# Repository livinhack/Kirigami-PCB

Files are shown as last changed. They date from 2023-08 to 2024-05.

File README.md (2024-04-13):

# Kirigami PCB Mod

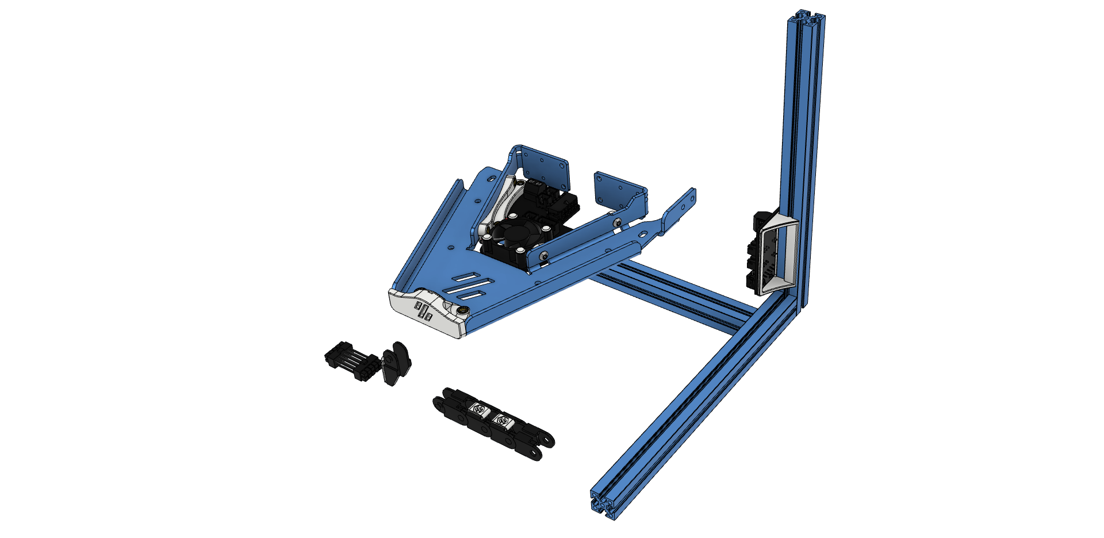
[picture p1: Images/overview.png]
Overview of the PCB's Title


This mod adds two PCBs ([Frame PCB](#frame-pcb), [Kirigami PCB](#kirigami-pcb)) and a cable ([Cable](#cable-and-chain)) to the V0.1/V0.2 that can aid in wire management and routing.

There are also optional things like a [Bed Fan](https://github.com/livinhack/Kirigami_PCB/tree/main/Optional/Bed_Fan) or a [Kirigami-Front](https://github.com/livinhack/Kirigami_PCB/tree/main/Optional/Front).

----

# Frame PCB
The frame PCB mounts on the side in the electronics bay of the printer and combines all cables into a single 10 pin Micro-Fit 3.0 connector. (With neopixel loop-through.)

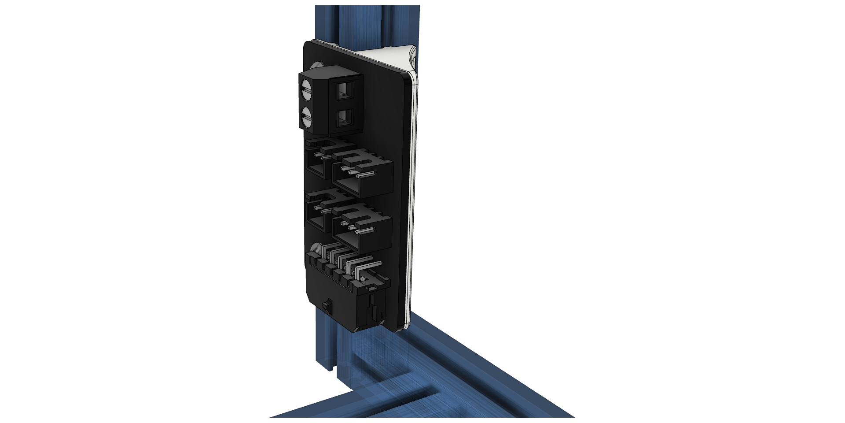
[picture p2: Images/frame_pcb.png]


## Frame PCB BOM
| Part | Quantity V1/V2 | Notes | LCSC Part Number | Link |
| --- | :-: | --- | --- |--- |
| 10 Pin Socket (Right Angle) | 1 | MOLEX 430451000 | C122421 | [lcsc](https://www.lcsc.com/product-detail/Wire-To-Board-Wire-To-Wire-Connector_MOLEX-430451000_C122421.html) |
| 2 pin JST XH | 2 | 2.5mm pitch | C158012 | [lcsc](https://lcsc.com/product-detail/Wire-To-Board-Wire-To-Wire-Connector_JST-Sales-America-B2B-XH-A-LF-SN_C158012.html) |
| 3 pin JST XH | 2 | 2.5mm pitch | C144394 | [lcsc](https://lcsc.com/product-detail/Wire-To-Board-Wire-To-Wire-Connector_JST-Sales-America-B3B-XH-A-LF-SN_C144394.html) |
| Screw Terminal | 1 | 5.08mm pitch | | [digikey](https://www.digikey.de/en/products/detail/metz-connect-usa-inc/31101102/7794830) |
| Screw M3x8 | 2 | | | |
| Nut M3 | 2 | | | |
----

# Kirigami PCB

Mounted on the Kirigami bed mount, this breaks out the 10 pin harness into all needed connectors.

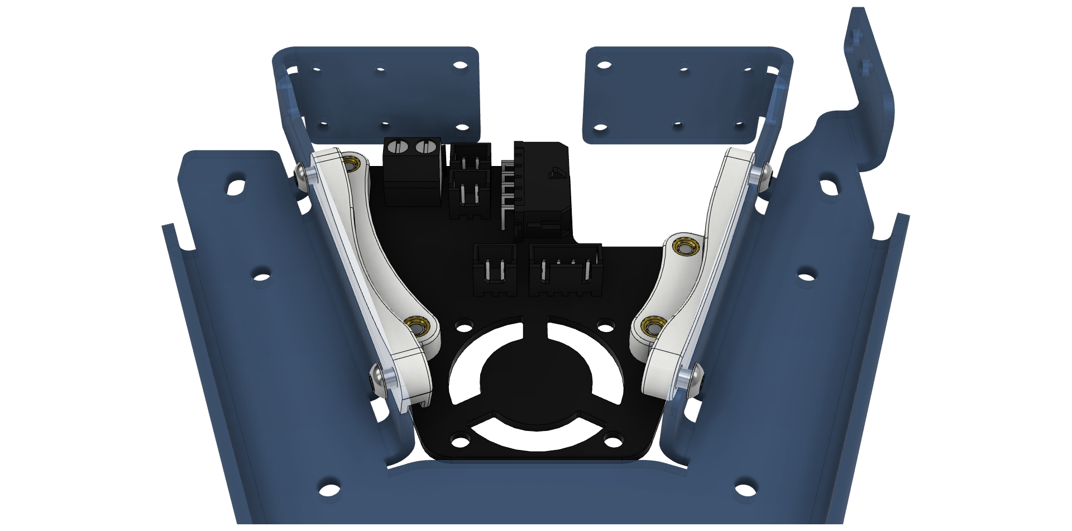
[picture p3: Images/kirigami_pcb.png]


## Kirigami PCB BOM
| Part | Quantity V1 | Quantity V2 | Notes | LCSC Part Number | Link |
| --- | :-: | :-: | --- | --- |--- |
| 10 Pin Socket (Right Angle) | 1 | 1 | MOLEX 430451000 | C122421 | [lcsc](https://www.lcsc.com/product-detail/Wire-To-Board-Wire-To-Wire-Connector_MOLEX-430451000_C122421.html) |
| 2 pin JST XH | 4 | 3 | B2B-XH | C158012 | [lcsc](https://lcsc.com/product-detail/Wire-To-Board-Wire-To-Wire-Connector_JST-Sales-America-B2B-XH-A-LF-SN_C158012.html) |
| 4 pin JST XH | 1 | 1 | B4B-XH | C144395 | [lcsc](https://lcsc.com/product-detail/Wire-To-Board-Wire-To-Wire-Connector_JST-Sales-America-B4B-XH-A-LF-SN_C144395.html) |
| Screw Terminal | | 1 | 5.08mm pitch | | [digikey](https://www.digikey.de/en/products/detail/metz-connect-usa-inc/31101102/7794830) |
| Screw M3x6 | 8 | 8 | *(Or M3x8)* | |
| Heat-Set Inserts | 8 | 8 | Voron-spec | |

### Optional Parts
| Part | Quantity | Notes | LCSC Part Number | Link |
| --- | :-: | --- | --- |--- |
| 0805 10uF Capacitor |  1 | Use if using BARE neopixel IC's. | C162422 | [lcsc](https://www.lcsc.com/product-detail/_Murata-Electronics-_C162422.html) |

## [Optional Bed Fan](https://github.com/livinhack/Kirigami_PCB/tree/main/Optional/Bed_Fan)

## [Optional Front](https://github.com/livinhack/Kirigami_PCB/tree/main/Optional/Front)

## [For the RGB lovers among us: Kirigami U.F.O.](https://github.com/livinhack/Kirigami_U.F.O)

### If you have a Neopixel in your Kirigami front, please note the following:

---

# Cable and chain

The Cable is a dual ended 10P (2x5) microfit cable. The connectors are wired 1:5, 6:10 so pin 1 connects to pin 5, pin 2 connects to pin 4 and so forth for all 10 pins.

*Only 2 of the 10 wires are shown for clarity. Connect each number to its opposite. (in it's row!)*

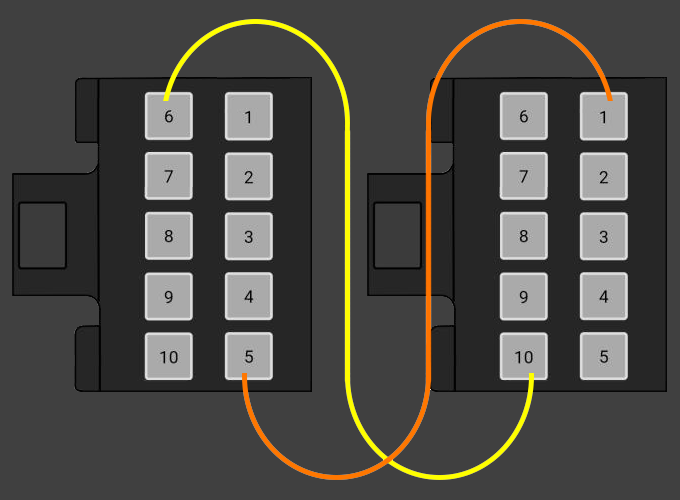
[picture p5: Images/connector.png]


Symbolic representation of the connection:

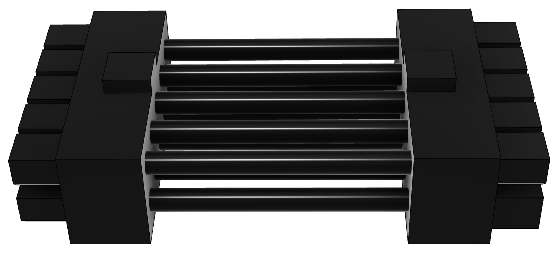
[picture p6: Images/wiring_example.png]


## Cable BOM
| Part | Quantity | Notes | LCSC Part Number | Link |
| --- | :-: | --- | --- |--- |
| 10 Pin Plug | 2 | Molex 430251400 | C259745 | [lcsc](https://www.lcsc.com/product-detail/Rectangular-Connectors-Housings_MOLEX-430251000_C259745.html) |
| Microfit Crimp | 20 | Molex 430300001 | C259786 | [lcsc](https://lcsc.com/product-detail/Line-Pressing-Terminals_MOLEX-430300001_C259786.html) |
| Wire | 10 | Smallest required AWG per respective function. | | PTFE/Silicone/Hefulon for motion rated |
### Note: Don't use 20 AWG wire on all ten!(!!!) It works, but it's a s**t job... Ask me how I know...
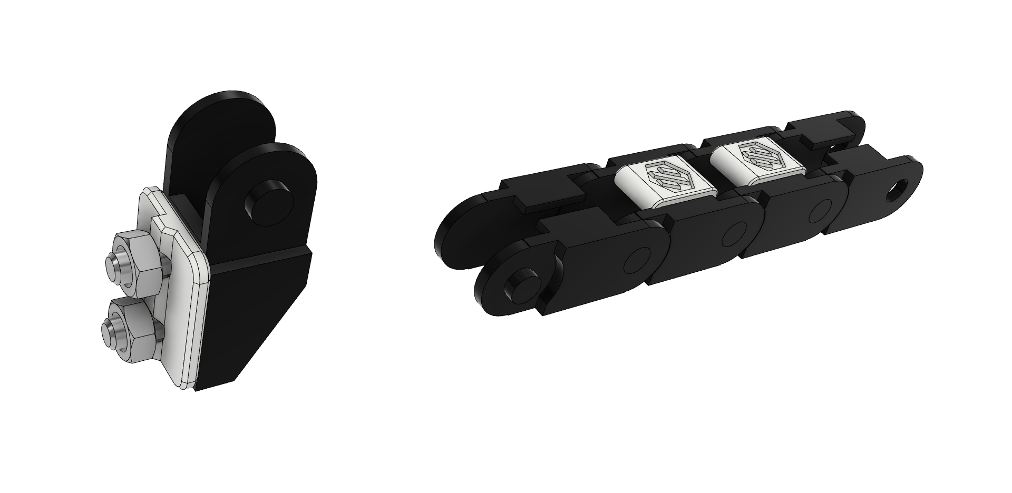
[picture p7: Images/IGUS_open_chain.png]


### Note: You don't need the chain-end spacer if your chain is "V0.1-spec"!
| Part  | Part Number  | Link |
| ---| --- |--- |
| Chain | E04.07.015.0 | [igus](https://www.igus.eu/iPro/iPro_01_0009_0001_GBen.htm?ArtNr=E04.07.015.0&c=DE&l=en) |
| | | [lecktor](https://lecktor.com/en/v0-cables-connectors/716-igus-v02-chain-e04070150-00716.html) |

-----

# Change Log #

## V2+:
 - Link to U.F.O. variant

## V2:
 - Moved Screw Terminal postition on Frame PCB and rearranged positons of the connectors + changing heater to Screw Terminal on the Kirigami PCB

## V1:
 - Initial Idea

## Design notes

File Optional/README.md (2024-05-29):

| Bed Fan | Front |
| --- |--- |
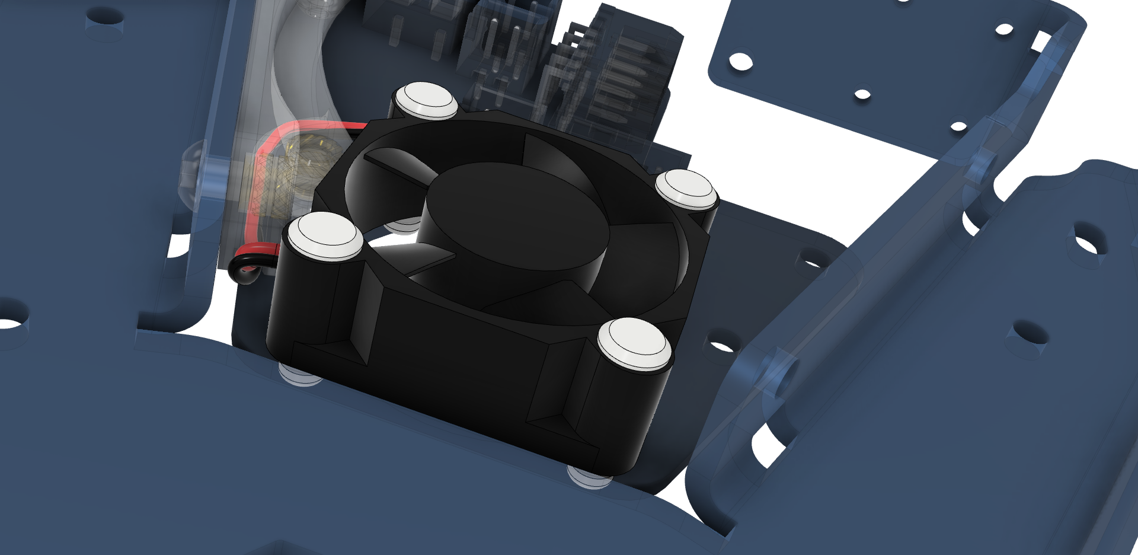
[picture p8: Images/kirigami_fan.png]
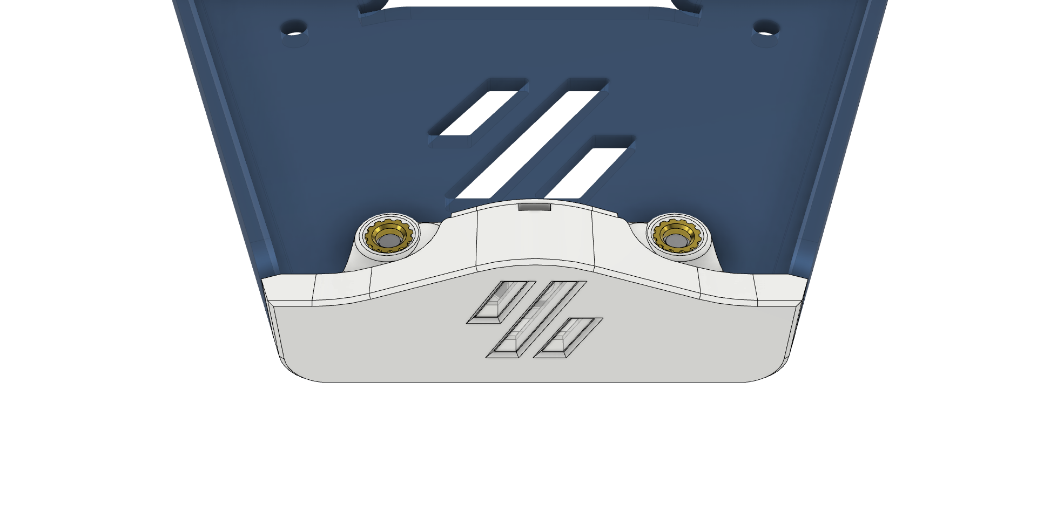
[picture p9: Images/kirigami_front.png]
|  |

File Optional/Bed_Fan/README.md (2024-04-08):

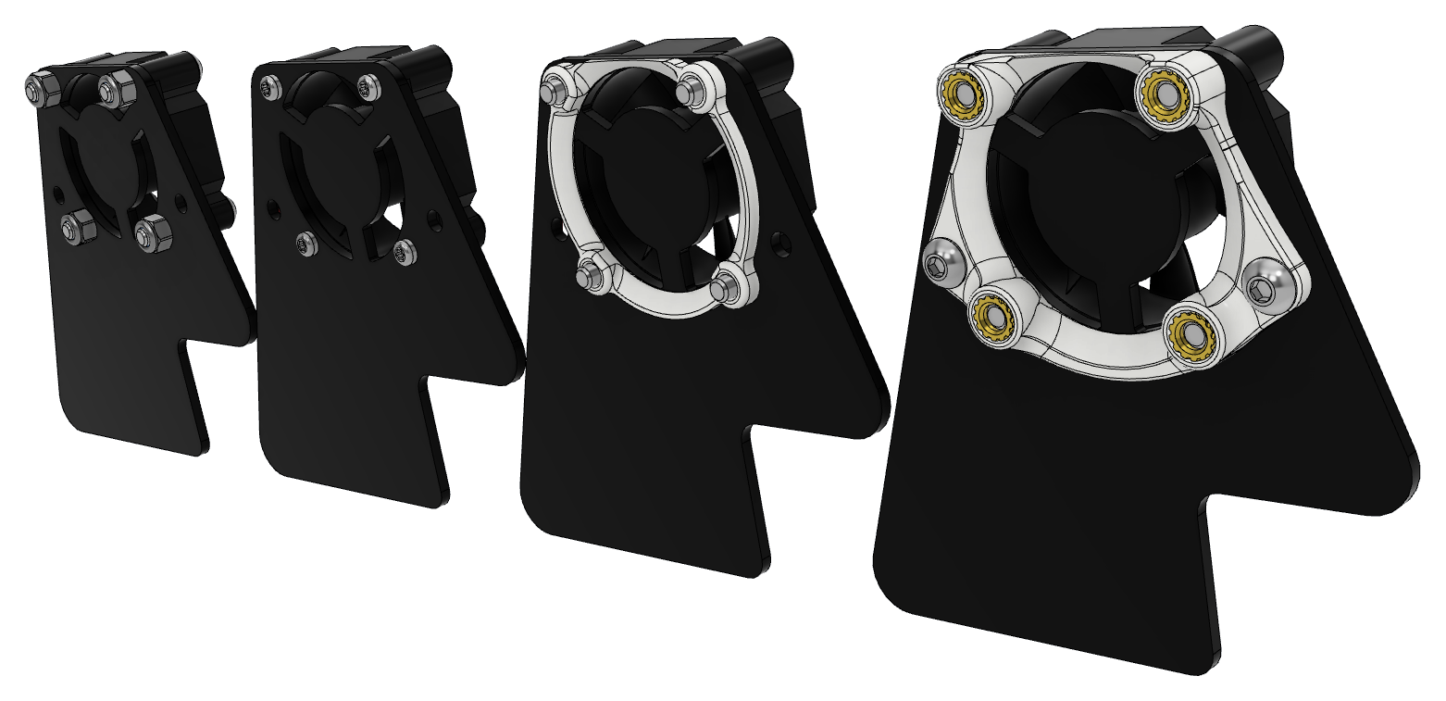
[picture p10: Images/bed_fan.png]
Title

## Bed Fan BOM
| Part | Opt. 1 Quantity | Opt. 2 Quantity | Opt. 3 Quantity | Opt. 4 Quantity | Notes |
| --- | :-: | :-: | :-: | :-: | --- |
| 3010 fan | 1 | 1 | 1 | 1 | Select *V* according to available sources |
| Screw M2x10 Self-tapping | | 4 | | | |
| Screw M3x8 | | | | 2 | |
| Screw M3x16 | 4 | | 4 | 4 | |
| Heat-Set Inserts | | | | 4 | Voron-spec |
| stop nut M3 | 4 | | | | |
### Note1:
I use Option 2 myself because this variant is the slimmest. However, it must also be individually adjusted, since tolerances, the respective fan and the screws must fit together. it works best when the pin just fits into the hole on the fan (twist-proof) and the screw hole is not too narrow.
THAT'S why I included the pin of the Option 2 as a single CAD file so that you can adjust it accordingly.

### Note2:
In the case of the UFO, Option 3 and 4 are omitted. These are intended for the original variant (non LED).

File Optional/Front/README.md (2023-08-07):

# Optional Front
Title
Since I put this Neopixel in the chain between the Klipper-Expander and the V0-Umbilical, this mod uses the same pinout.

Title

## Front BOM
| Part | Quantity | Notes | Link |
| --- | :-: | --- | --- |
| WS2812 | 1 | | [aliexpress](https://de.aliexpress.com/item/1005001527124508.html) |
| Wire | 4 | *Thin!* | |
| Screw M3x6 | 2 | *(Or M3x8)* | |
| Heat-Set Inserts | 2 | Voron-spec  | |

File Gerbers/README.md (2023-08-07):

# Attention!
## Choose these Options!

Title

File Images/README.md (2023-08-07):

| . | . | . | . |
| --- |--- | --- |--- |
| Title | Title | Title | Title |
| Title | Title | Title | Title |
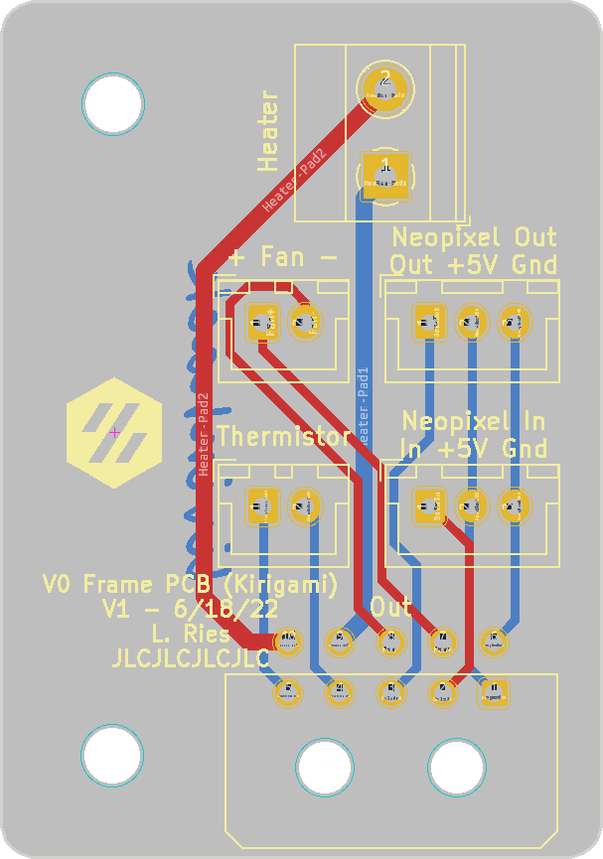
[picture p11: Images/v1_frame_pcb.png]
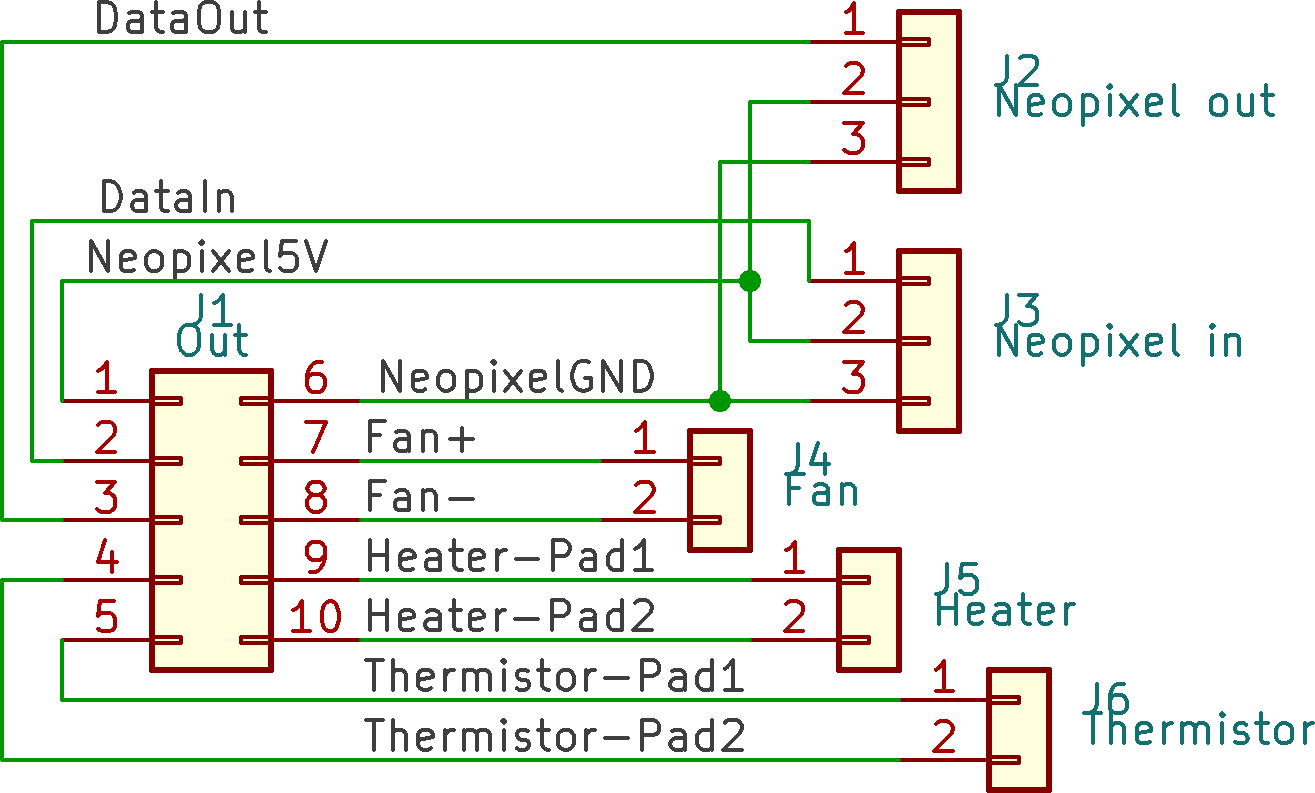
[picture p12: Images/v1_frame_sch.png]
| Title | Title |  |  |
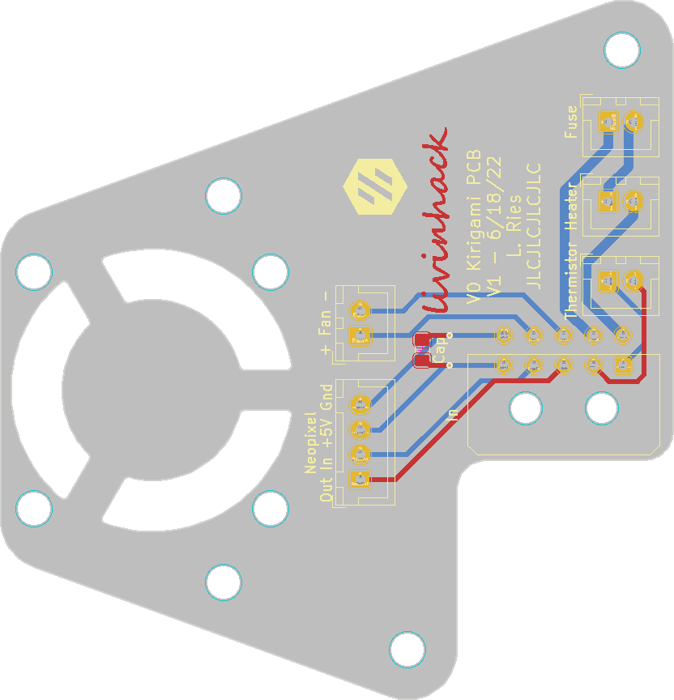
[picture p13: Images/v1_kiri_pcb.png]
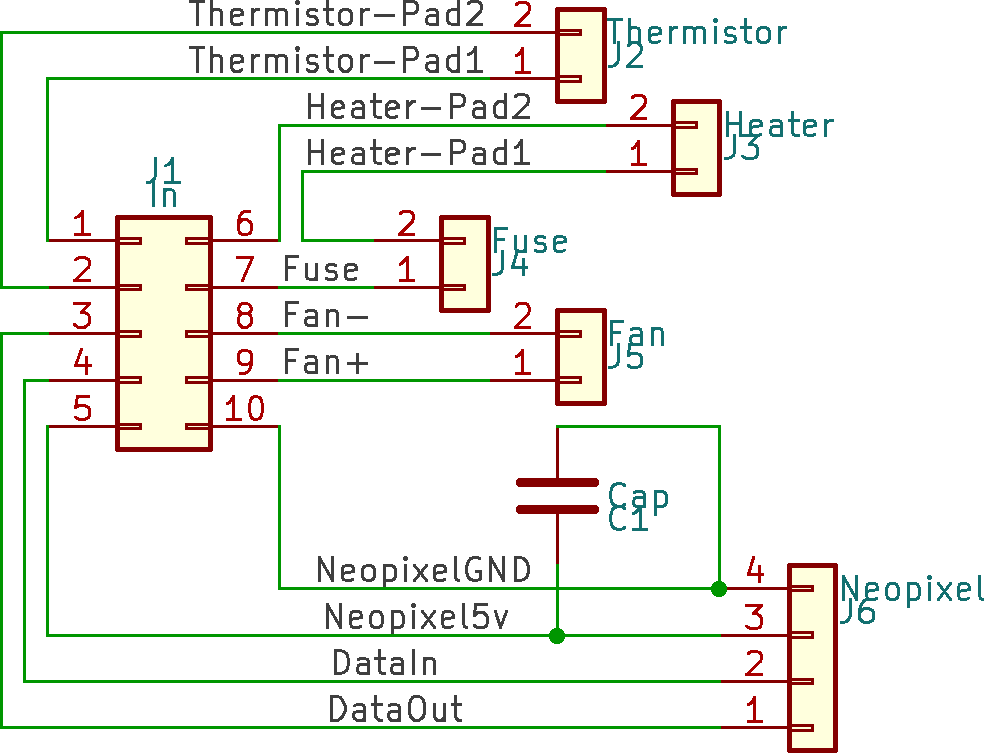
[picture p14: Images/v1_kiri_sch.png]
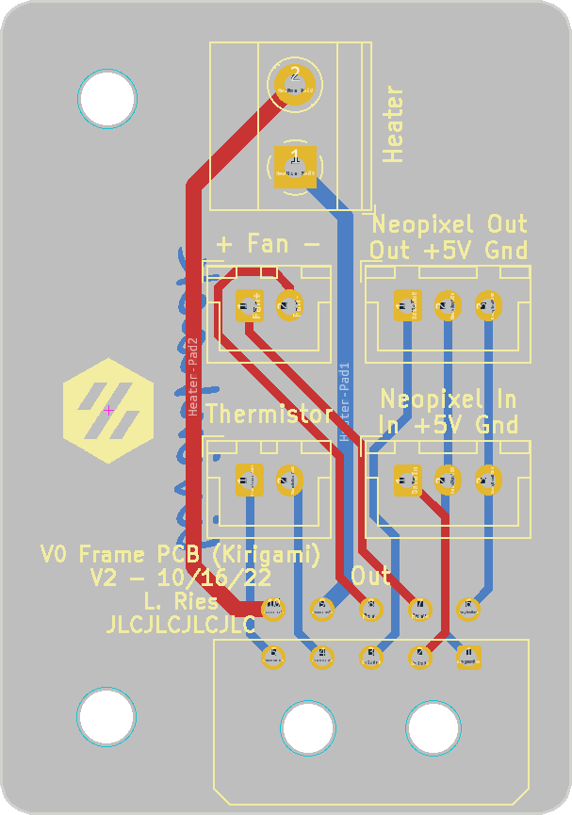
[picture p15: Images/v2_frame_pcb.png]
|  |  |  | Title |
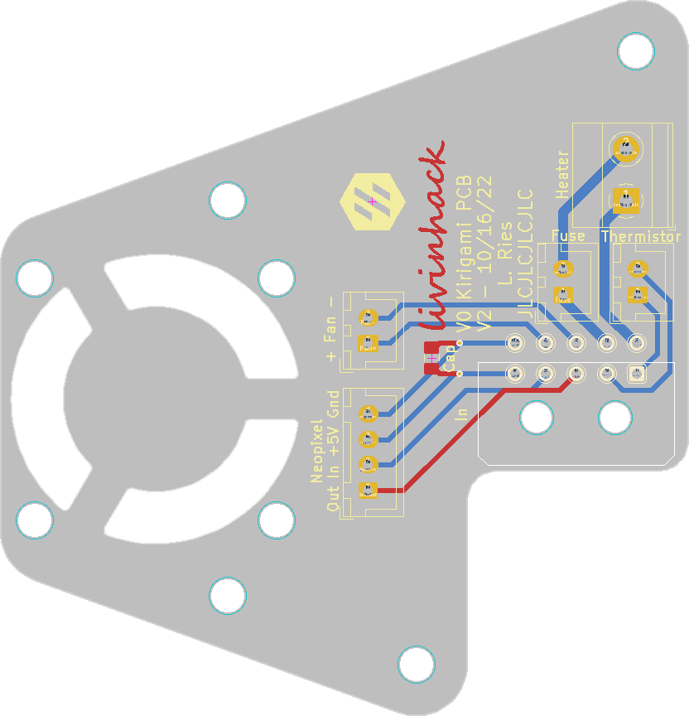
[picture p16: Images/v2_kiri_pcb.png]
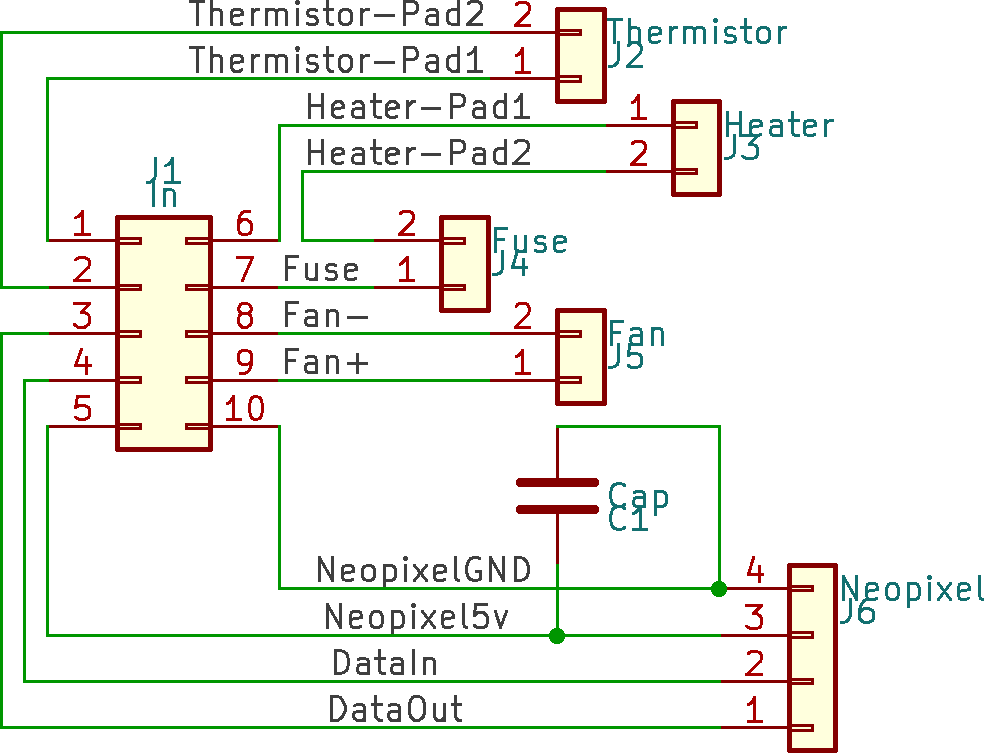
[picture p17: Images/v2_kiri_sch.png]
|  |  | Title | |

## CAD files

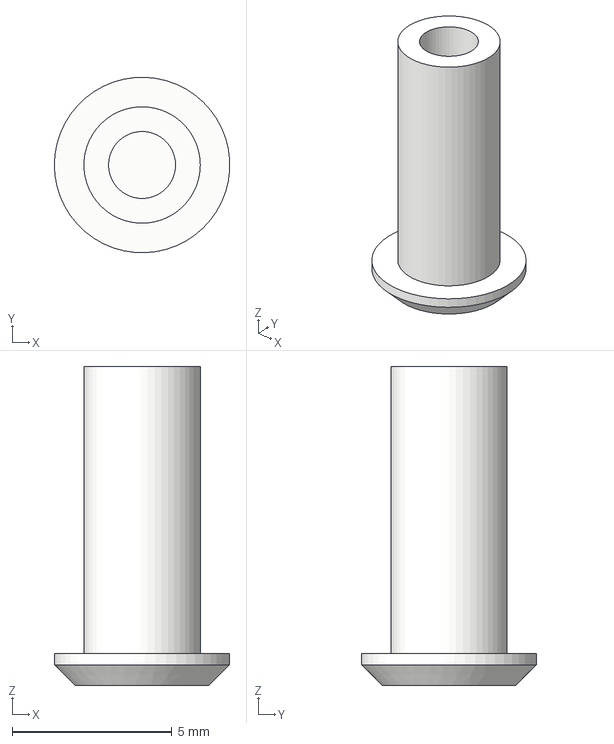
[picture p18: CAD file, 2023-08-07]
Optional/Bed_Fan/CAD/option_2_pin.step
5.49 x 5.50 x 10.0 mm

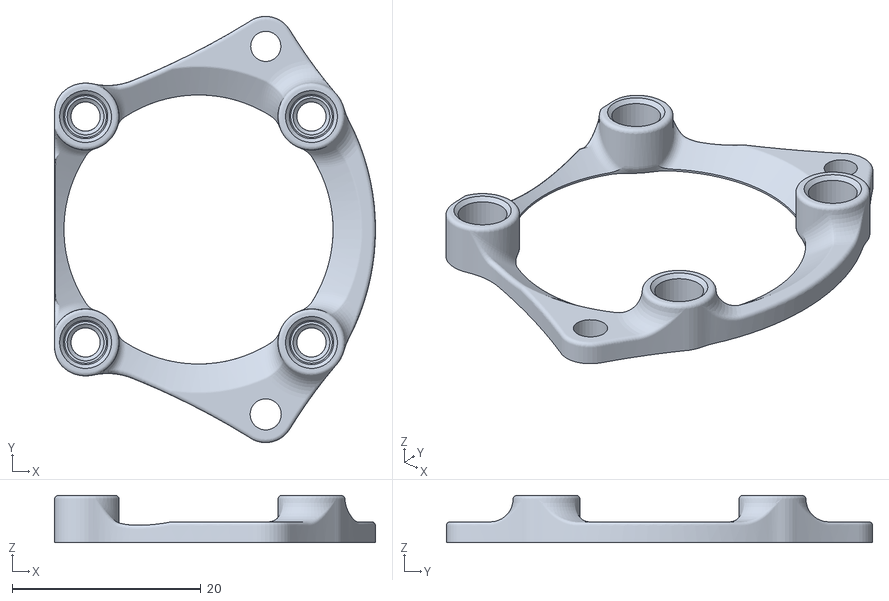
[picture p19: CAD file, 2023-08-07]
Optional/Bed_Fan/STLs/mounting_option_4.stl
34.0 x 45.1 x 5.00

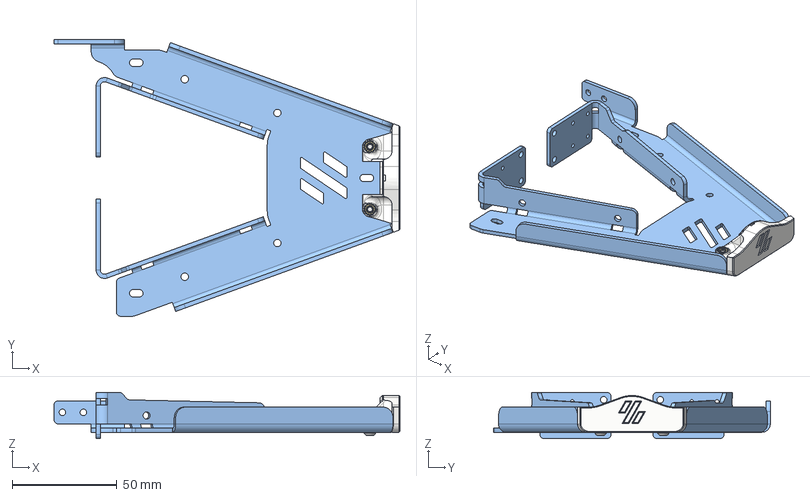
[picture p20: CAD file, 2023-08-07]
Optional/Front/CAD/kirigami_front.step
165.1 x 132.0 x 22.0 mm
lid
WS2812
front
diff (1)
M3 Threaded Insert (1)^VORON Clockwork_X Carriage673029 (1) (8) (1)
M3 Threaded Insert (1)^VORON Clockwork_X Carriage673029 (1) (9) (1)
m3x6 (5) (1)
m3x6 (4) (1)

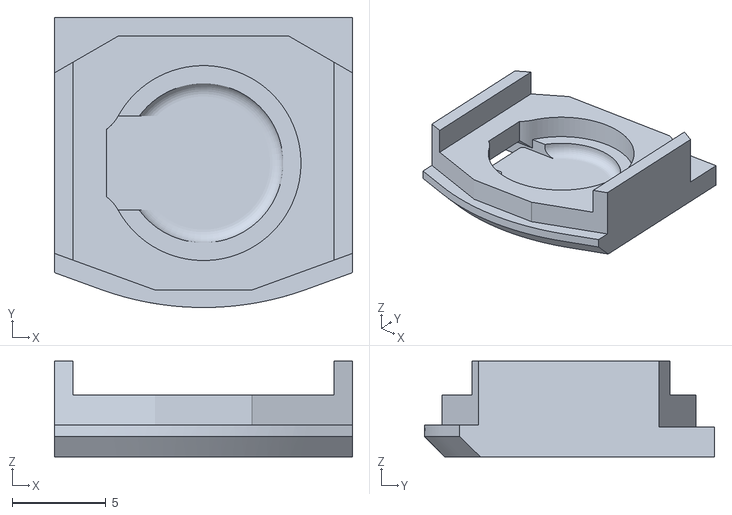
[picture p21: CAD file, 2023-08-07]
Optional/Front/STLs/lid.stl
15.9 x 15.5 x 5.10

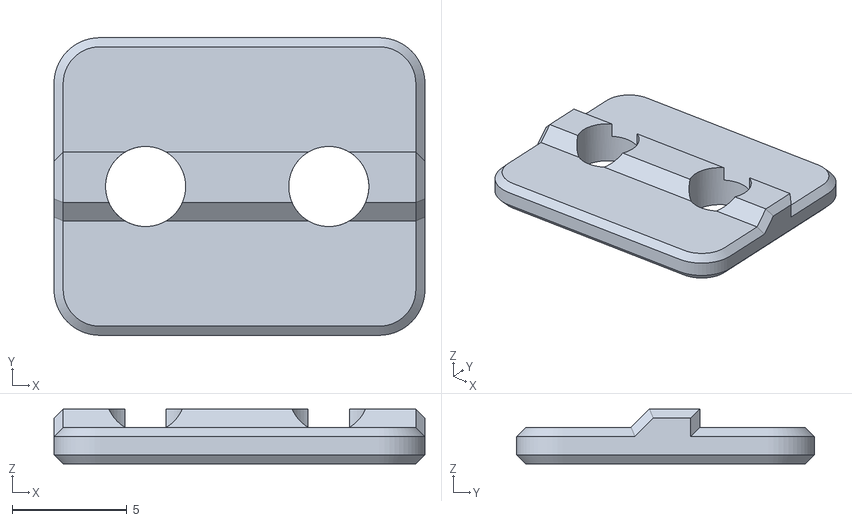
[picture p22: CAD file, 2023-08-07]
STLs/chain_end_spacer_(v0.2).stl
16.2 x 13.0 x 2.40

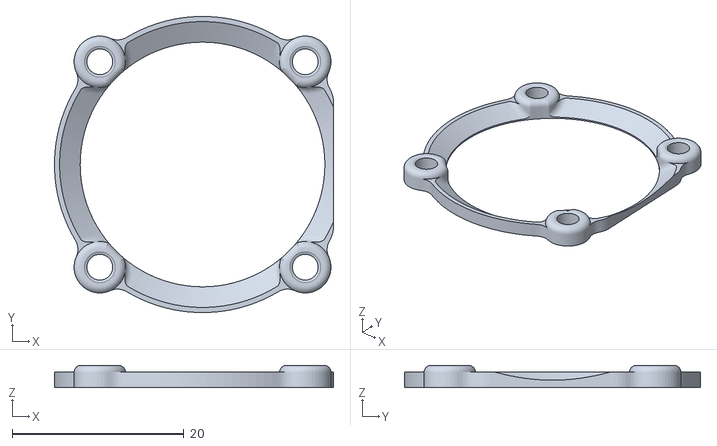
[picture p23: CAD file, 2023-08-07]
Optional/Bed_Fan/STLs/mounting_option_3.stl
32.5 x 34.5 x 2.60

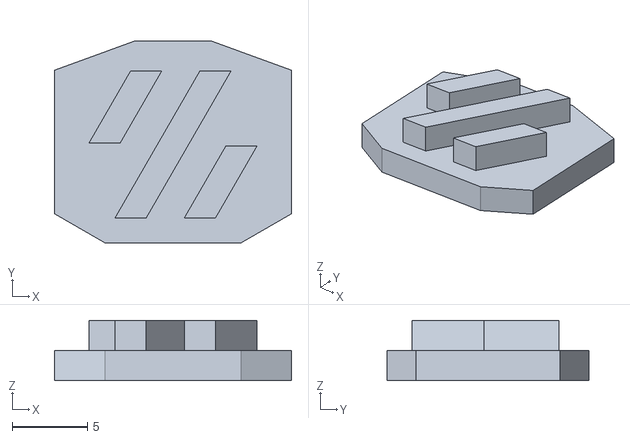
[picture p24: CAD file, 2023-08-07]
Optional/Front/STLs/diffuser.stl
15.8 x 13.4 x 4.00

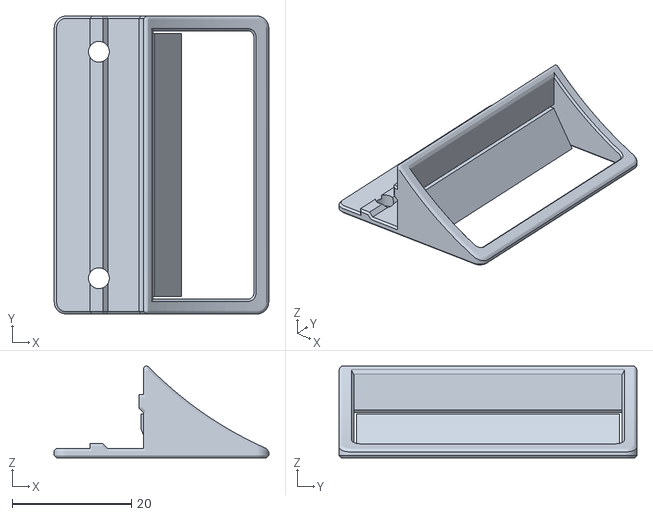
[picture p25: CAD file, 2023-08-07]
STLs/frame_pcb_mount.stl
36.0 x 50.0 x 15.4

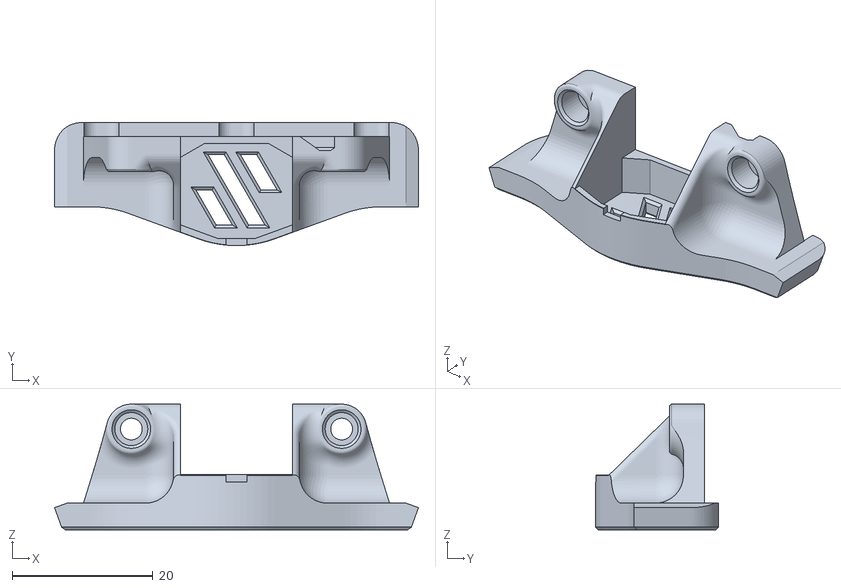
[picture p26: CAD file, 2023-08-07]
Optional/Front/STLs/front.stl
51.8 x 17.5 x 17.9

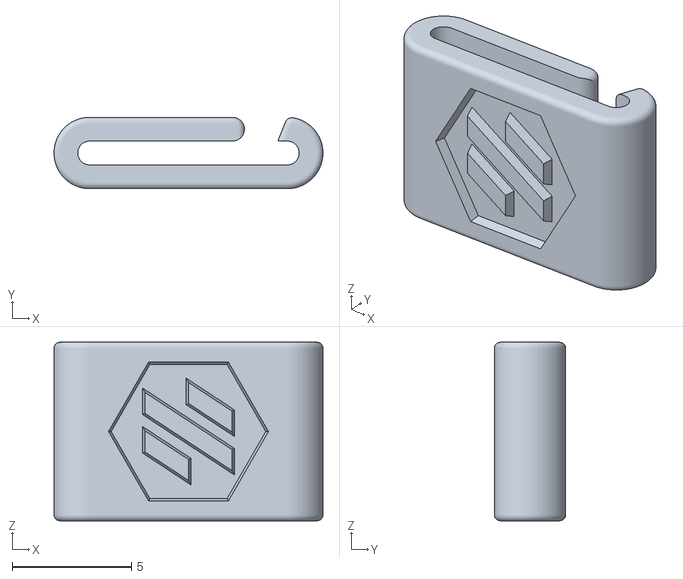
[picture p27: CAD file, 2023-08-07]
STLs/chain_link_lid.stl
11.3 x 3.00 x 7.50

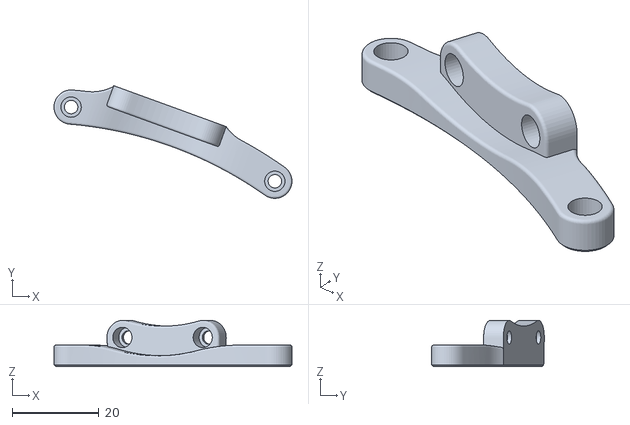
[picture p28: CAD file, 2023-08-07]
STLs/r_mount.stl
54.9 x 26.0 x 10.7

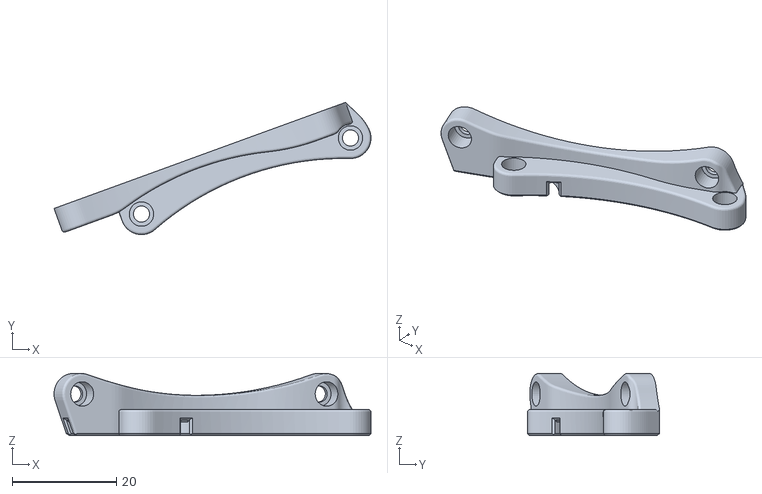
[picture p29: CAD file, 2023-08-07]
STLs/l_mount.stl
60.9 x 25.4 x 11.9

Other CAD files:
Optional/Bed_Fan/STLs/mounting_option_2.stl
Optional/Bed_Fan/CAD/bed_fan.f3d
Optional/Bed_Fan/CAD/option_2_pin.f3d
Optional/Front/CAD/kirigami_front.f3d

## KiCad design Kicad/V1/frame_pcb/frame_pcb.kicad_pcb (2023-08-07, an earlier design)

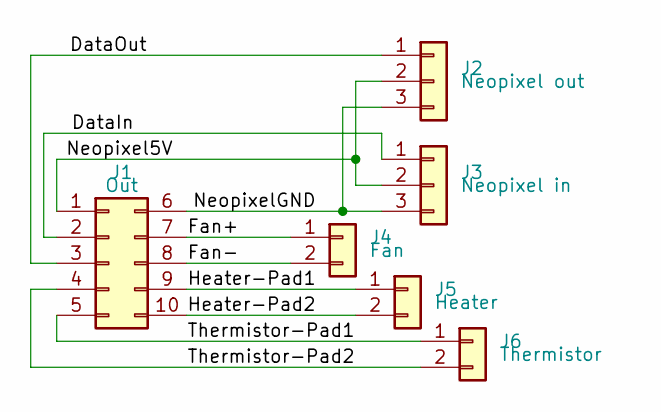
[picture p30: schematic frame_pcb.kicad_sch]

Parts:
J1: Out; Molex_Micro-Fit_3.0_43045-1000_2x05_P3.00mm_Horizontal
J2: Neopixel out; JST_XH_B3B-XH-A_1x03_P2.50mm_Vertical
J3: Neopixel in; JST_XH_B3B-XH-A_1x03_P2.50mm_Vertical
J4: Fan; JST_XH_B2B-XH-A_1x02_P2.50mm_Vertical
J5: Heater; METZ CONNECT USA Inc. - TERM BLK 2P SIDE ENT 5.08MM PCB
J6: Thermistor; JST_XH_B2B-XH-A_1x02_P2.50mm_Vertical

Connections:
/DataIn: J1.2, J3.1
/DataOut: J1.3, J2.1
/Fan+: J1.7, J4.1
/Fan-: J1.8, J4.2
/Heater-Pad1: J1.9, J5.1
/Heater-Pad2: J1.10, J5.2
/Neopixel5V: J1.1, J2.2, J3.2
/NeopixelGND: J1.6, J2.3, J3.3
/Thermistor-Pad1: J1.5, J6.1
/Thermistor-Pad2: J1.4, J6.2

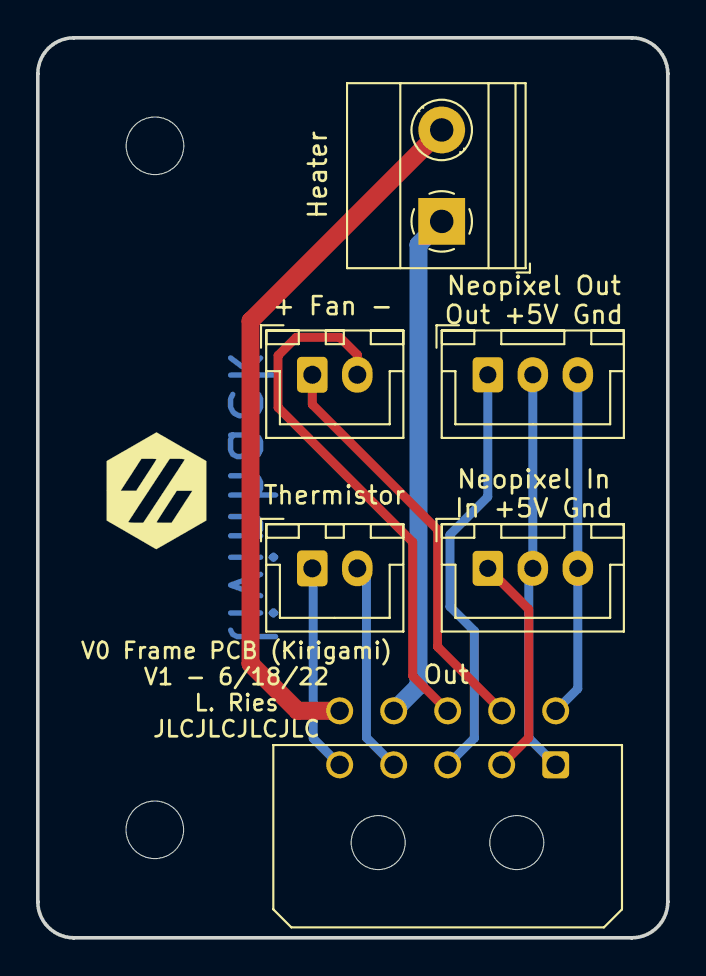
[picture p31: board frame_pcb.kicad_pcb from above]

Board: 2 copper layers, 35.0 x 50.0 mm, 8 parts (0 on the bottom side), 10 nets.

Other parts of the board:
H1, H2: MountingHole_3.2mm_M3

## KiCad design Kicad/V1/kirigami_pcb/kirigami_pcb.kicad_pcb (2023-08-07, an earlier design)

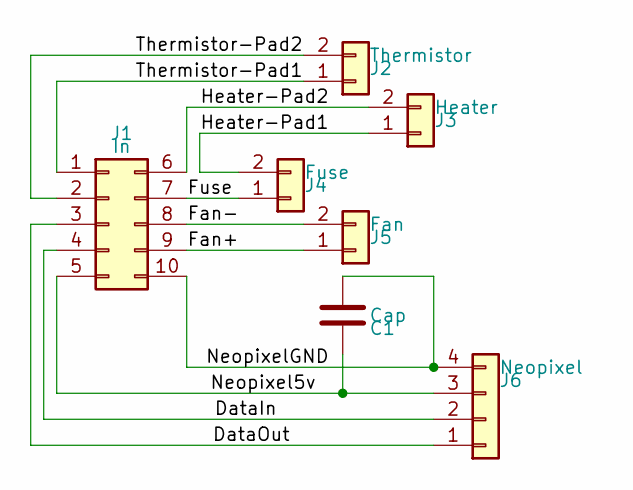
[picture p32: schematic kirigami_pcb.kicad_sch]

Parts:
C1: Cap; C_0805_2012Metric_Pad1.18x1.45mm_HandSolder
J1: In; Molex_Micro-Fit_3.0_43045-1000_2x05_P3.00mm_Horizontal
J2: Thermistor; JST_XH_B2B-XH-A_1x02_P2.50mm_Vertical
J3: Heater; JST_XH_B2B-XH-A_1x02_P2.50mm_Vertical
J4: Fuse; JST_XH_B2B-XH-A_1x02_P2.50mm_Vertical
J5: Fan; JST_XH_B2B-XH-A_1x02_P2.50mm_Vertical
J6: Neopixel; JST_XH_B4B-XH-A_1x04_P2.50mm_Vertical

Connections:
/DataIn: J1.4, J6.2
/DataOut: J1.3, J6.1
/Fan+: J1.9, J5.1
/Fan-: J1.8, J5.2
/Fuse: J1.7, J4.1
/Heater-Pad1: J3.1, J4.2
/Heater-Pad2: J1.6, J3.2
/Neopixel5v: C1.1, J1.5, J6.3
/NeopixelGND: C1.2, J1.10, J6.4
/Thermistor-Pad1: J1.1, J2.1
/Thermistor-Pad2: J1.2, J2.2

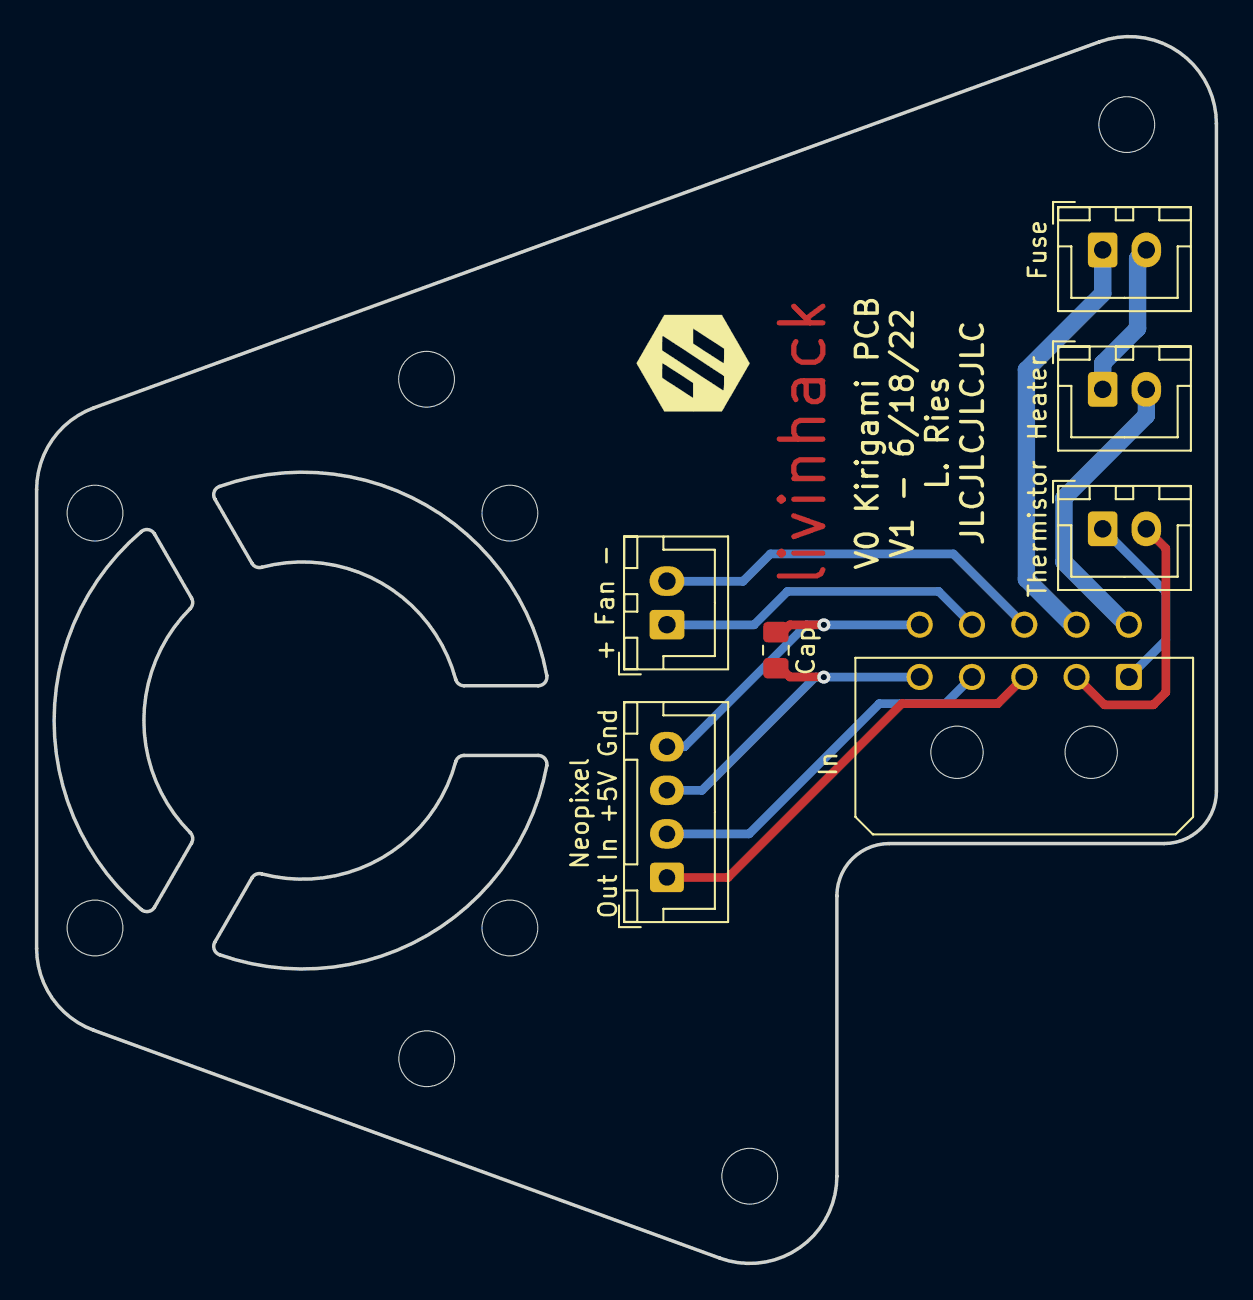
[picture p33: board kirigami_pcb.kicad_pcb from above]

Board: 2 copper layers, 67.7 x 70.4 mm, 15 parts (0 on the bottom side), 11 nets.

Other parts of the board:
H1, H2, H3, H4, H5, H6, H7, H8: MountingHole_3.2mm_M3
